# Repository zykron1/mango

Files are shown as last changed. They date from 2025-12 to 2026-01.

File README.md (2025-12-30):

# MANGO
An ESP32-S3 based flight computer with an external flash, imu, barometer, magnetometer, 4 servo ports, and 4 pyrotechnic channels with MOSFETs. Designed for Aerospace applications.
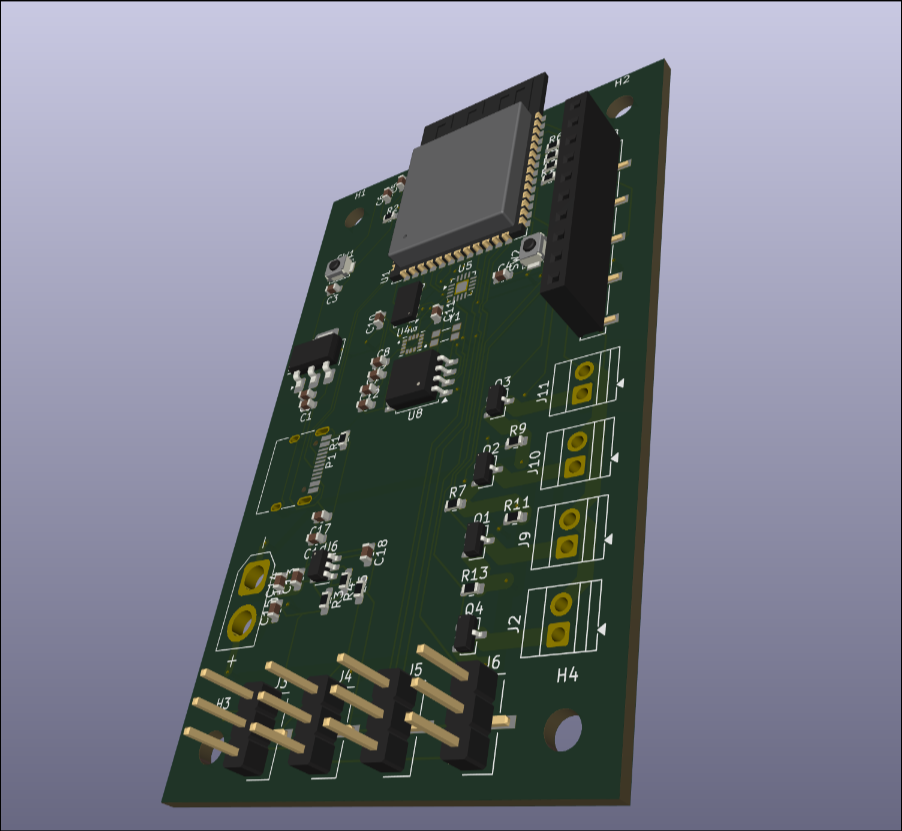
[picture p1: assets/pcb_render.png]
render


## Key Features
 - Dual core Xtensa microcontroller
 - 4 Servo Outputs
 - 4 High current mosfet switches for pyrotechnic channels
 - External 16 MB flash for flight logging
 - IMU, Magnetometer, and Barometer for orientation and state estimation
 - External expansion header with space for an I2C bus, 4 extra GPIO pins, and 2 pairs of power

## Schematic
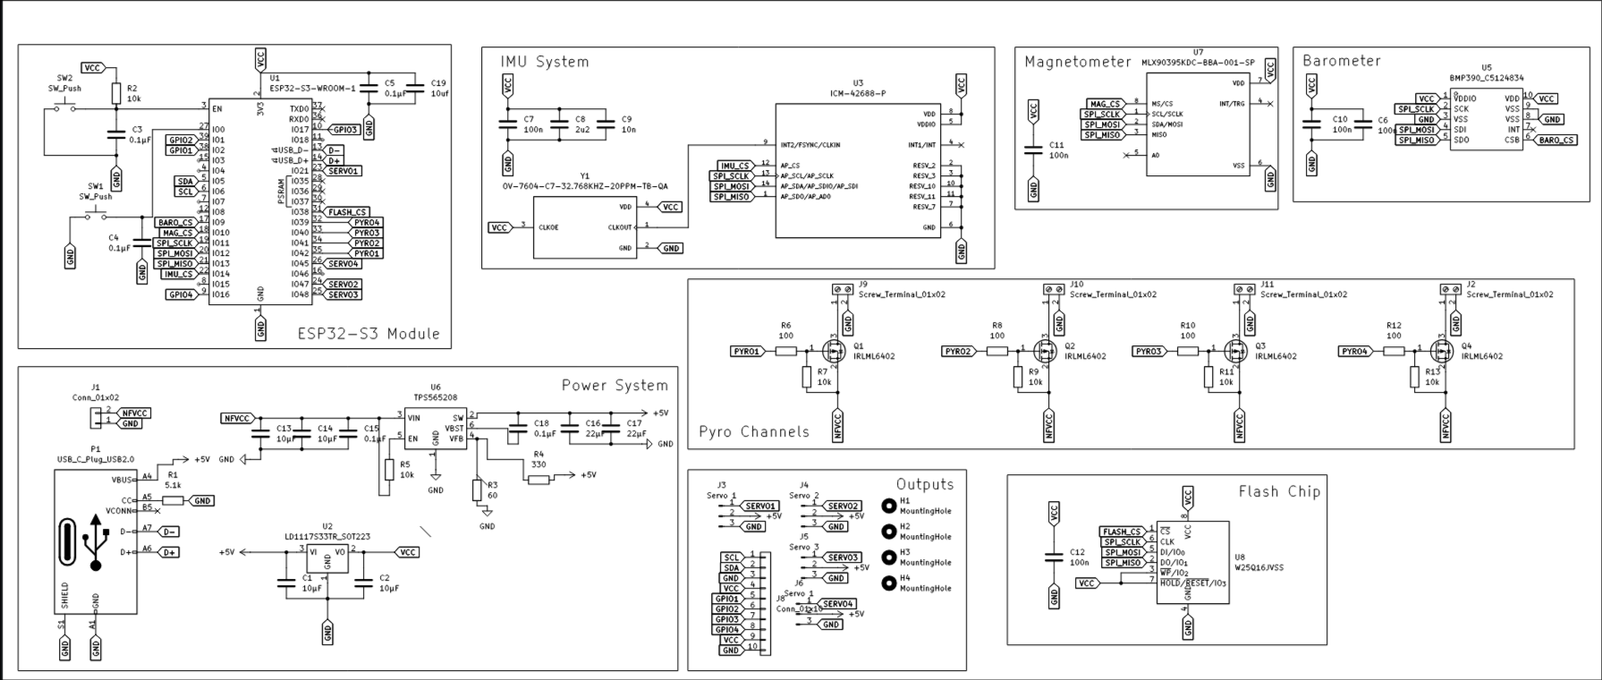
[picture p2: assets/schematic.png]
schematic


## PCB
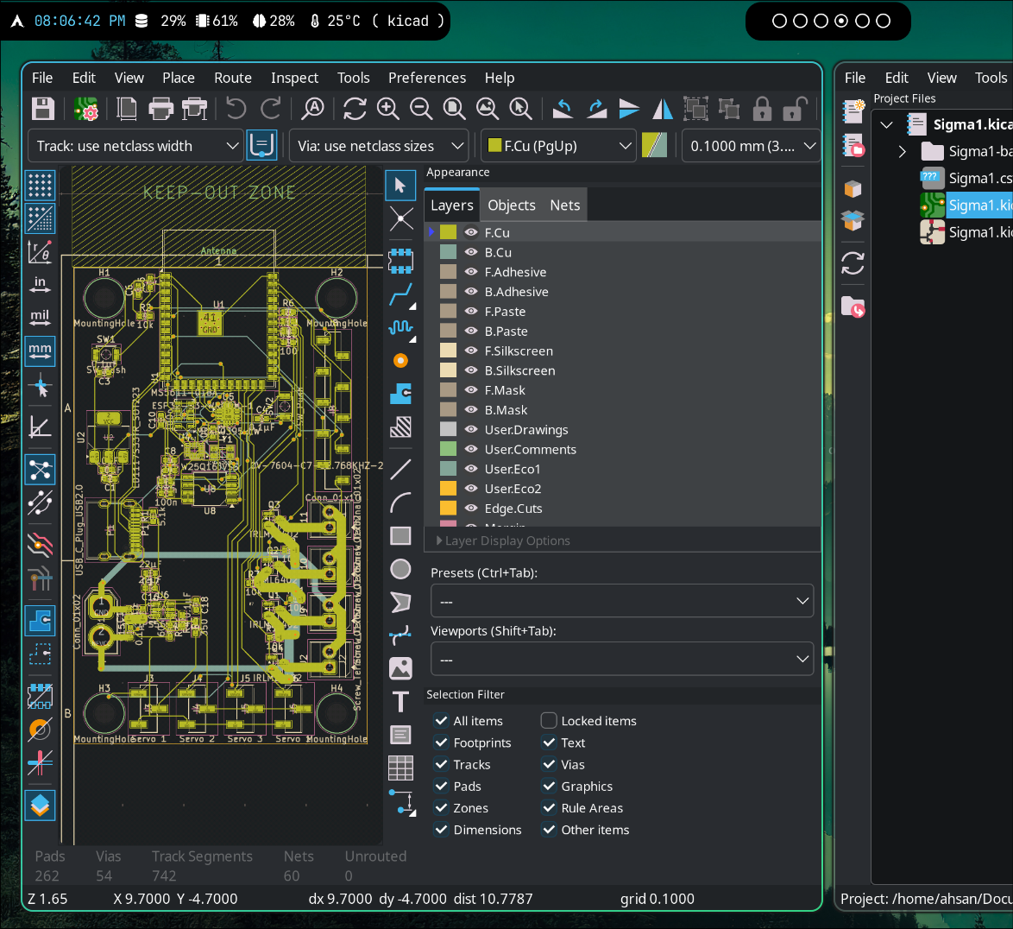
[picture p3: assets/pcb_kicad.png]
pcb


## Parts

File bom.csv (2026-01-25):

Product | Link | Cost Per Item | Quantity | Total | Note
(pcb AND STENCIL) | https://github.com/zykron1/mango/blob/main/pcb/production/MANGO_final.zip | $19.53 | 1 | $16.17
10µF | https://www.digikey.com/en/products/detail/murata-electronics/GRT188R61E106ME13D/5417024 | $0.25 | 4 | $1.00
100n | https://www.digikey.com/en/products/detail/murata-electronics/GCM188R71E104KA57D/3845251 | $0.25 | 5 | $1.25
0.1µF | https://www.digikey.com/en/products/detail/murata-electronics/GCM188R71E104KA57D/3845251 | $0.25 | 5 | $1.25
22µF | https://www.digikey.com/en/products/detail/yageo/CC0603MRX5R6BB226/5195721 | $0.65 | 2 | $1.30
10uf | https://www.digikey.com/en/products/detail/murata-electronics/GRT188R61E106ME13D/5417024 | $0.25 | 1 | $0.25
2u2 | https://www.digikey.com/en/products/detail/samsung-electro-mechanics/CL10B225KP8NNNC/3886792 | $0.08 | 1 | $0.08
10n | https://www.digikey.com/en/products/detail/murata-electronics/GRM1555C1E103JE01D/16707175 | $0.14 | 1 | $0.14
Conn_01x02 | https://www.digikey.com/en/products/detail/amphenol-icc-fci-/10129378-916001BLF/7915965 | $0.30 | 1 | $0.30
Screw_Terminal_01x02 | https://tinkersphere.com/breadboard-perfboard-prototyping/476-2-pole-screw-terminal-breadboard-compatible.html | $0.75 | 4 | $3.00 | Not requesting Funding for this
Servo 1 | sharing from 10 |  | 2 | 0
Servo 2 | sharing from 10 |  | 1 | 0
Servo 3 | sharing from 10 |  | 1 | 0
Conn_01x10 | sharing from 10 |  | 1 | 0
USB_C_Plug_USB2.0 | https://www.digikey.com/en/products/detail/amphenol-cs-commercial-products/124019772112A/13683231 | $1.96 | 1 | $1.96
IRLML6402 | https://www.digikey.com/en/products/detail/infineon-technologies/IRLML6402TRPBF/811437 | $0.42 | 4 | $1.68
5.1k | https://www.digikey.com/en/products/detail/yageo/RC0603FR-105K1L/14287630 | $0.10 | 1 | $0.10
100 | https://www.digikey.com/en/products/detail/yageo/RC0603FR-10100RL/12756410 | $0.10 | 4 | $0.40
<<<<<<< HEAD
10k | https://www.digikey.com/en/products/detail/yageo/RC0603FR-1010KL/12756418 | $0.10 | 6 | $0.60
60 | https://www.digikey.com/en/products/detail/bourns-inc/CR0603-FX-60R4ELF/CR0603-FX-60R4ELFCT-ND/4247821 | $0.10 | 1 | $0.10
330 | https://www.digikey.com/en/products/detail/vishay-dale/CRCW0603330RJNEAC/7928482 | $0.10 | 1 | $0.10
=======
10k | https://www.digikey.com/en/products/detail/yageo/RC0603FR-1010KL/12756418 | $0.10 | 7 | $0.70
3.3uh | https://www.digikey.com/en/products/detail/murata-electronics/LQM21PN3R3MG0D/19560375 | $0.17 | 1 | $0.17
54.9k | https://www.digikey.com/en/products/detail/yageo/RC0603FR-0754K9L/727298 | $0.10 | 1 | $0.10
>>>>>>> d75fabc (added inductor and used recomended texas instruments resistors)
TS-1088R-02026 | https://www.digikey.com/en/products/detail/e-switch/TL3365AF180QG/5964420 | $0.21 | 2 | $0.42
ESP32-S3-WROOM-1 | https://www.digikey.com/en/products/detail/espressif-systems/ESP32-S3-WROOM-1-N8/15200089 | $5.49 | 1 | $5.49
LD1117S33TR_SOT223 | https://www.digikey.com/en/products/detail/stmicroelectronics/LD1117S33TR/585766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 | $0.34 | 1 | $0.34
ICM-42688-P | https://www.digikey.com/en/products/detail/tdk-invensense/ICM-42688-P/10824934 | $4.67 | 1 | $4.67
BMP390_C5124834 | https://www.digikey.com/en/products/detail/bosch-sensortec/BMP390/16164575 | $3.15 | 1 | $3.15
TPS565208 | https://www.digikey.com/en/products/detail/texas-instruments/TPS565208DDCR/7776393 | $1.38 | 1 | $1.38
MLX90395KDC-BBA-001-SP | https://www.digikey.com/en/products/detail/melexis-technologies-nv/MLX90395KDC-BBA-101-RE/12330246 | $2.85 | 1 | $2.85
W25Q16JVSS | https://www.digikey.com/en/products/detail/winbond-electronics/W25Q16JVSSIQ/6193769 | $0.60 | 1 | $0.60
OV-7604-C7-32.768KHZ-20PPM-TB-QA | https://www.digikey.com/en/products/detail/micro-crystal-ag/OV-7604-C7-32-768KHZ-20PPM-TB-QA/10499163 | $2.07 | 1 | $2.07
Subtotal | $50.65
DigiKey Shipping Cost | $6.99
Digikey Tarrif Cost | $0.80
Total Parts Cost | $42.41 | (TAXES)
Total Board Cost | $58.58
Asking For: 62 dollars(JLC prices are variable)

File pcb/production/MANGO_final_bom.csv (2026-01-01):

Designator | Footprint | Quantity | Value | LCSC Part #
C1, C13, C14, C2 | 0603 | 4 | 10µF
C10, C11, C12, C6, C7 | 0603 | 5 | 100n
C15, C18, C3, C4, C5 | 0603 | 5 | 0.1µF
C16, C17 | 0603 | 2 | 22µF
C19 | 0603 | 1 | 10uf
C8 | 0603 | 1 | 2u2
C9 | 0603 | 1 | 10n
J1 | AMASS_XT30U-F_1x02_P5.0mm_Vertical | 1 | Conn_01x02
J10, J11, J2, J9 | TerminalBlock_Xinya_XY308-2.54-2P_1x02_P2.54mm_Horizontal | 4 | Screw_Terminal_01x02
J3, J6 | PinHeader_1x03_P2.54mm_Vertical | 2 | Servo 1
J4 | PinHeader_1x03_P2.54mm_Vertical | 1 | Servo 2
J5 | PinHeader_1x03_P2.54mm_Vertical | 1 | Servo 3
J8 | PinHeader_1x10_P2.54mm_Vertical | 1 | Conn_01x10
P1 | USB_C_Receptacle_Amphenol_124019772112A | 1 | USB_C_Plug_USB2.0
Q1, Q2, Q3, Q4 | SOT-23 | 4 | IRLML6402
R1 | 0603 | 1 | 5.1k
R10, R12, R6, R8 | 0603 | 4 | 100
R11, R13, R2, R5, R7, R9 | 0603 | 6 | 10k
R3 | 0603 | 1 | 60
R4 | 0603 | 1 | 330
SW1, SW2 | SW_TL3365AF180QG | 2 | SW_Push
U1 | ESP32-S3-WROOM-1 | 1 | ESP32-S3-WROOM-1
U2 | SOT-223-3_TabPin2 | 1 | LD1117S33TR_SOT223
U3 | PQFN50P300X250X97-14N | 1 | ICM-42688-P
U5 | LGA-10_L2.0-W2.0-P0.50-BL | 1 | BMP390_C5124834 | C5124834
U6 | SOT-23-6 | 1 | TPS565208
U7 | SOIC127P600X172-8N | 1 | MLX90395KDC-BBA-001-SP
U8 | SOIC-8_5.3x5.3mm_P1.27mm | 1 | W25Q16JVSS
Y1 | OSC_OV-7604-C7-32.768KHZ-20PPM-TB-QA | 1 | OV-7604-C7-32.768KHZ-20PPM-TB-QA

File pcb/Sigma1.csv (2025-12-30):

Reference | Qty | Value | DNP | Exclude from BOM | Exclude from Board | Footprint | Datasheet
C1,C2,C13,C14 | 4 | 10µF |  |  |  | Capacitor_SMD:C_0603_1608Metric | ~
C3,C4,C15,C18 | 4 | 0.1µF |  |  |  | Capacitor_SMD:C_0603_1608Metric | ~
C5,C6 | 2 | C |  |  |  | Capacitor_SMD:C_0603_1608Metric | ~
C7,C10,C11,C12 | 4 | 100n |  |  |  | Capacitor_SMD:C_0603_1608Metric | ~
C8 | 1 | 2u2 |  |  |  | Capacitor_SMD:C_0603_1608Metric | ~
C9 | 1 | 10n |  |  |  | Capacitor_SMD:C_0603_1608Metric | ~
C16,C17 | 2 | 22µF |  |  |  | Capacitor_SMD:C_0603_1608Metric | ~
H1,H2,H3,H4 | 4 | MountingHole |  | Excluded from BOM |  | MountingHole:MountingHole_3.2mm_M3 | ~
J1 | 1 | Conn_01x02 |  |  |  | Connector_AMASS:AMASS_XT30U-F_1x02_P5.0mm_Vertical | ~
J2,J9,J10,J11 | 4 | Screw_Terminal_01x02 |  |  |  | TerminalBlock:TerminalBlock_Xinya_XY308-2.54-2P_1x02_P2.54mm_Horizontal | ~
J3,J6 | 2 | Servo 1 |  |  |  | Connector_PinHeader_2.54mm:PinHeader_1x03_P2.54mm_Vertical_SMD_Pin1Left | ~
J4 | 1 | Servo 2 |  |  |  | Connector_PinHeader_2.54mm:PinHeader_1x03_P2.54mm_Vertical_SMD_Pin1Left | ~
J5 | 1 | Servo 3 |  |  |  | Connector_PinHeader_2.54mm:PinHeader_1x03_P2.54mm_Vertical_SMD_Pin1Left | ~
J8 | 1 | Conn_01x10 |  |  |  | Connector_PinSocket_2.54mm:PinSocket_1x10_P2.54mm_Vertical_SMD_Pin1Left | ~
P1 | 1 | USB_C_Plug_USB2.0 |  |  |  | Connector_USB:USB_C_Receptacle_HRO_TYPE-C-31-M-12 | https://www.usb.org/sites/default/files/documents/usb_type-c.zip
Q1,Q2,Q3,Q4 | 4 | IRLML6402 |  |  |  | Package_TO_SOT_SMD:SOT-23 | https://www.infineon.com/dgdl/irlml6402pbf.pdf?fileId=5546d462533600a401535668d5c2263c
R1 | 1 | 5.1k |  |  |  | Resistor_SMD:R_0603_1608Metric | ~
R2,R7,R9,R11,R13 | 5 | 10k |  |  |  | Resistor_SMD:R_0603_1608Metric | ~
R3 | 1 | 60 |  |  |  | Resistor_SMD:R_0603_1608Metric_Pad0.98x0.95mm_HandSolder | ~
R4 | 1 | 350 |  |  |  | Resistor_SMD:R_0603_1608Metric_Pad0.98x0.95mm_HandSolder | ~
R5 | 1 | 10k |  |  |  | Resistor_SMD:R_0603_1608Metric_Pad0.98x0.95mm_HandSolder | ~
R6,R8,R10,R12 | 4 | 100 |  |  |  | Resistor_SMD:R_0603_1608Metric | ~
SW1,SW2 | 2 | SW_Push |  |  |  | Button_Switch_SMD:SW_SPST_B3U-1000P-B | ~
U1 | 1 | ESP32-S3-WROOM-1 |  |  |  | RF_Module:ESP32-S3-WROOM-1 | https://www.espressif.com/sites/default/files/documentation/esp32-s3-wroom-1_wroom-1u_datasheet_en.pdf
U2 | 1 | LD1117S33TR_SOT223 |  |  |  | Package_TO_SOT_SMD:SOT-223-3_TabPin2 | http://www.st.com/st-web-ui/static/active/en/resource/technical/document/datasheet/CD00000544.pdf
U3 | 1 | ICM-42688-P |  |  |  | ICM:PQFN50P300X250X97-14N
U4 | 1 | MS5611-01BA |  |  |  | Package_LGA:LGA-8_3x5mm_P1.25mm | https://www.te.com/commerce/DocumentDelivery/DDEController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
U5 | 1 | MLX90395xLW |  |  |  | Package_DFN_QFN:QFN-16-1EP_3x3mm_P0.5mm_EP1.675x1.675mm | https://www.melexis.com/en/documents/documentation/datasheets/datasheet-mlx90395
U6 | 1 | TPS565208 |  |  |  | Package_TO_SOT_SMD:SOT-23-6 | http://www.ti.com/lit/ds/symlink/tps565208.pdf
U8 | 1 | W25Q16JVSS |  |  |  | Package_SO:SOIC-8_5.3x5.3mm_P1.27mm | https://www.winbond.com/hq/support/documentation/levelOne.jsp?__locale=en&DocNo=DA00-W25Q16JV.1
Y1 | 1 | OV-7604-C7-32.768KHZ-20PPM-TB-QA |  |  |  | OV7604C7:OSC_OV-7604-C7-32.768KHZ-20PPM-TB-QA

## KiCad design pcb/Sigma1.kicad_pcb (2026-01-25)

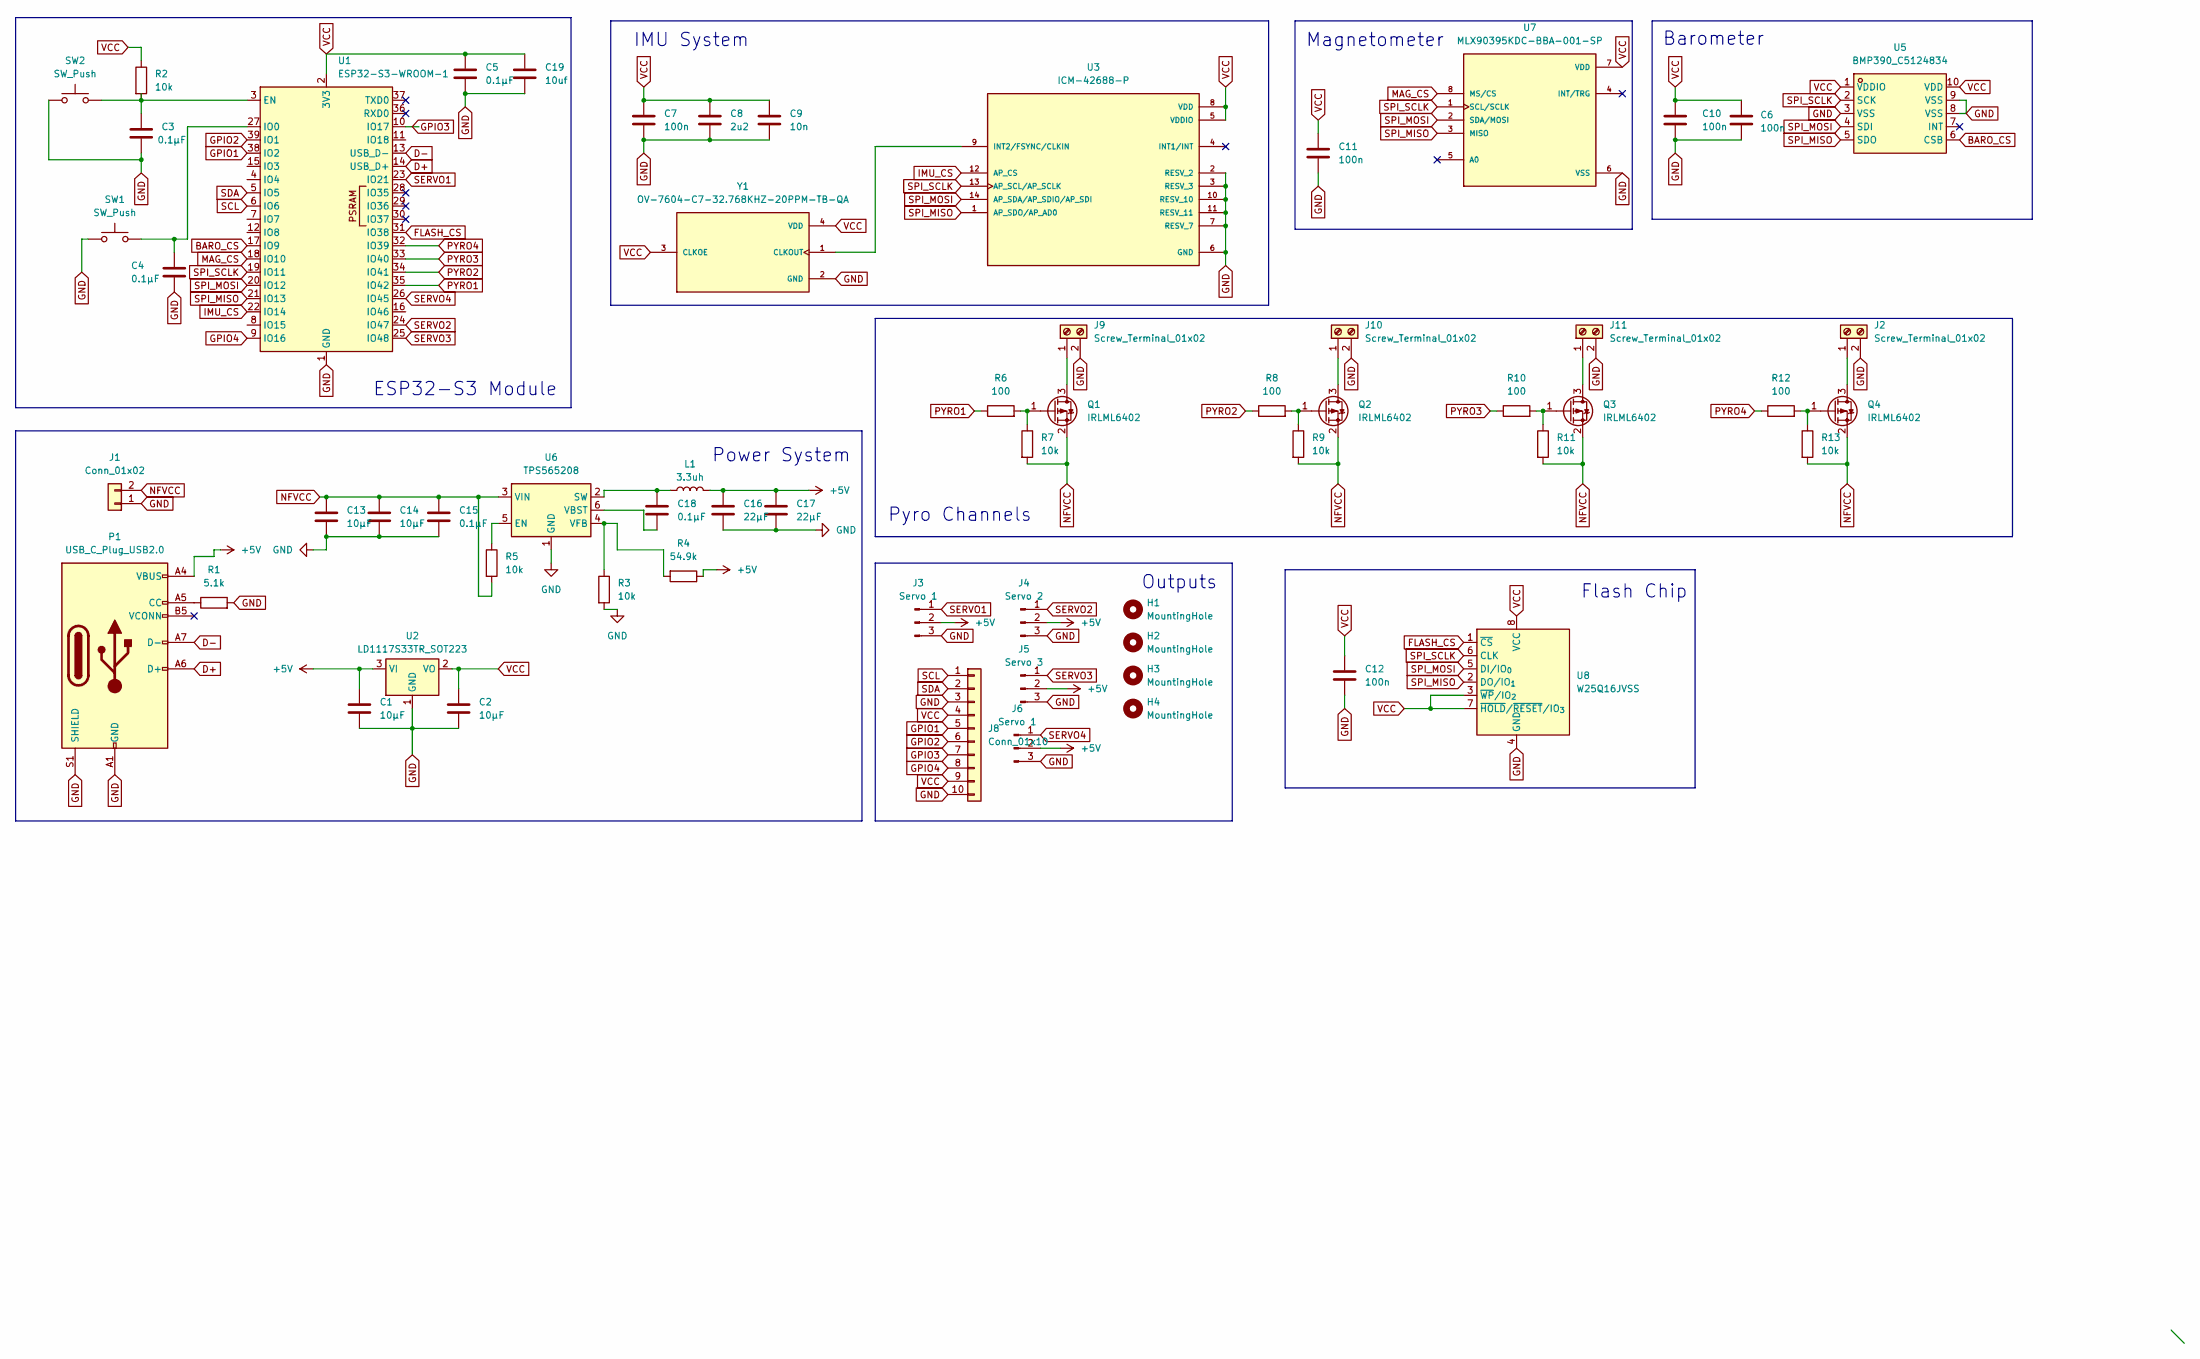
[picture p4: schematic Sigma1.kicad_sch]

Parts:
C1, C2, C13, C14: 10µF; C_0603_1608Metric
C3, C4, C15, C18: 0.1µF; C_0603_1608Metric
C5: 0.1μF; C_0603_1608Metric
C6, C7, C10, C11, C12: 100n; C_0603_1608Metric
C8: 2u2; C_0603_1608Metric
C9: 10n; C_0603_1608Metric
C16, C17: 22µF; C_0603_1608Metric
C19: 10uf; C_0603_1608Metric
H1, H2, H3, H4: MountingHole; MountingHole_3.2mm_M3
J1: Conn_01x02; AMASS_XT30U-F_1x02_P5.0mm_Vertical
J2, J9, J10, J11: Screw_Terminal_01x02; TerminalBlock_Xinya_XY308-2.54-2P_1x02_P2.54mm_Horizontal
J3, J6: Servo 1; PinHeader_1x03_P2.54mm_Vertical
J4: Servo 2; PinHeader_1x03_P2.54mm_Vertical
J5: Servo 3; PinHeader_1x03_P2.54mm_Vertical
J8: Conn_01x10; PinHeader_1x10_P2.54mm_Vertical
L1: 3.3uh; L_0805_2012Metric
P1: USB_C_Plug_USB2.0; USB_C_Receptacle_Amphenol_124019772112A
Q1, Q2, Q3, Q4: IRLML6402; SOT-23
R1: 5.1k; R_0603_1608Metric
R2, R7, R9, R11, R13: 10k; R_0603_1608Metric
R3, R5: 10k; R_0603_1608Metric_Pad0.98x0.95mm_HandSolder
R4: 54.9k; R_0603_1608Metric_Pad0.98x0.95mm_HandSolder
R6, R8, R10, R12: 100; R_0603_1608Metric
SW1, SW2: SW_Push; SW_TL3365AF180QG
U1: ESP32-S3-WROOM-1
U2: LD1117S33TR_SOT223; SOT-223-3_TabPin2
U3: ICM-42688-P; PQFN50P300X250X97-14N; PARTREV 1.2
U5: BMP390_C5124834; LGA-10_L2.0-W2.0-P0.50-BL; LCSC Part C5124834
U6: TPS565208; SOT-23-6
U7: MLX90395KDC-BBA-001-SP; SOIC127P600X172-8N; PARTREV 6.0
U8: W25Q16JVSS; SOIC-8_5.3x5.3mm_P1.27mm
Y1: OV-7604-C7-32.768KHZ-20PPM-TB-QA; OSC_OV-7604-C7-32.768KHZ-20PPM-TB-QA; PARTREV 4.4

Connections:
+5V: C1.1, C16.1, C17.1, J3.2, J4.2, J5.2, J6.2, L1.1, P1.A4 (VBUS), P1.A9 (VBUS), P1.B4 (VBUS), P1.B9 (VBUS), R4.1, U2.3 (VI)
BARO_CS: U1.17 (IO9), U5.6 (CSB)
D+: P1.A6 (D+), U1.14 (USB_D+)
D-: P1.A7 (D-), U1.13 (USB_D-)
FLASH_CS: U1.31 (IO38), U8.1 (~CS)
GND: C1.2, C2.2, C3.2, C4.2, C5.2, C6.2, C7.2, C8.2, C9.2, C10.2, C11.2, C12.2, C13.2, C14.2, C15.2, C16.2, C17.2, C19.2, J1.1, J2.2, J3.3, J4.3, J5.3, J6.3, J8.3, J8.10, J9.2, J10.2, J11.2, P1.A1 (GND), P1.A12 (GND), P1.B1 (GND), P1.B12 (GND), P1.S1 (SHIELD), R1.2, R3.2, SW1.1, SW2.1, U1.1 (GND), U1.40 (GND), U1.41 (GND), U2.1 (GND), U3.2 (RESV_2), U3.3 (RESV_3), U3.6 (GND), U3.7 (RESV_7), U3.10 (RESV_10), U3.11 (RESV_11), U5.3 (VSS), U5.8 (VSS), U5.9 (VSS), U6.1 (GND), U7.6 (VSS), U8.4 (GND), Y1.2 (GND)
GPIO1: J8.5, U1.38 (IO2)
GPIO2: J8.6, U1.39 (IO1)
GPIO3: J8.7, U1.10 (IO17)
GPIO4: J8.8, U1.9 (IO16)
IMU_CS: U1.22 (IO14), U3.12 (AP_CS)
MAG_CS: U1.18 (IO10), U7.8 (MS/CS)
NFVCC: C13.1, C14.1, C15.1, J1.2, Q1.2 (S), Q2.2 (S), Q3.2 (S), Q4.2 (S), R5.2, R7.2, R9.2, R11.2, R13.2, U6.3 (VIN)
unnamed: J2.1, Q4.3 (D)
unnamed: J9.1, Q1.3 (D)
unnamed: J10.1, Q2.3 (D)
unnamed: J11.1, Q3.3 (D)
unnamed: P1.A5 (CC), R1.1
unnamed: Q1.1 (G), R6.2, R7.1
unnamed: Q2.1 (G), R8.2, R9.1
unnamed: Q3.1 (G), R10.2, R11.1
unnamed: Q4.1 (G), R12.2, R13.1
unnamed: C3.1, R2.2, SW2.2, U1.3 (EN)
unnamed: C4.1, SW1.2, U1.27 (IO0)
unnamed: U3.9 (INT2/FSYNC/CLKIN), Y1.1 (CLKOUT)
unnamed: R5.1, U6.5 (EN)
unnamed: C18.1, L1.2, U6.2 (SW)
unnamed: C18.2, U6.6 (VBST)
unnamed: R3.1, R4.2, U6.4 (VFB)
PYRO1: R6.1, U1.35 (IO42)
PYRO2: R8.1, U1.34 (IO41)
PYRO3: R10.1, U1.33 (IO40)
PYRO4: R12.1, U1.32 (IO39)
SCL: J8.1, U1.6 (IO6)
SDA: J8.2, U1.5 (IO5)
SERVO1: J3.1, U1.23 (IO21)
SERVO2: J4.1, U1.24 (IO47)
SERVO3: J5.1, U1.25 (IO48)
SERVO4: J6.1, U1.26 (IO45)
SPI_MISO: U1.21 (IO13), U3.1 (AP_SDO/AP_AD0), U5.5 (SDO), U7.3 (MISO), U8.2 (DO/IO_{1})
SPI_MOSI: U1.20 (IO12), U3.14 (AP_SDA/AP_SDIO/AP_SDI), U5.4 (SDI), U7.2 (SDA/MOSI), U8.5 (DI/IO_{0})
SPI_SCLK: U1.19 (IO11), U3.13 (AP_SCL/AP_SCLK), U5.2 (SCK), U7.1 (SCL/SCLK), U8.6 (CLK)
VCC: C2.1, C5.1, C6.1, C7.1, C8.1, C9.1, C10.1, C11.1, C12.1, C19.1, J8.4, J8.9, R2.1, U1.2 (3V3), U2.2 (VO), U3.5 (VDDIO), U3.8 (VDD), U5.1 (VDDIO), U5.10 (VDD), U7.7 (VDD), U8.3 (~WP/IO_{2}), U8.7 (~HOLD/~RESET/IO_{3}), U8.8 (VCC), Y1.3 (CLKOE), Y1.4 (VDD)

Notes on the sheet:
ESP32-S3 Module
Flash Chip
Magnetometer
Outputs
Pyro Channels
Power System
Barometer
IMU System

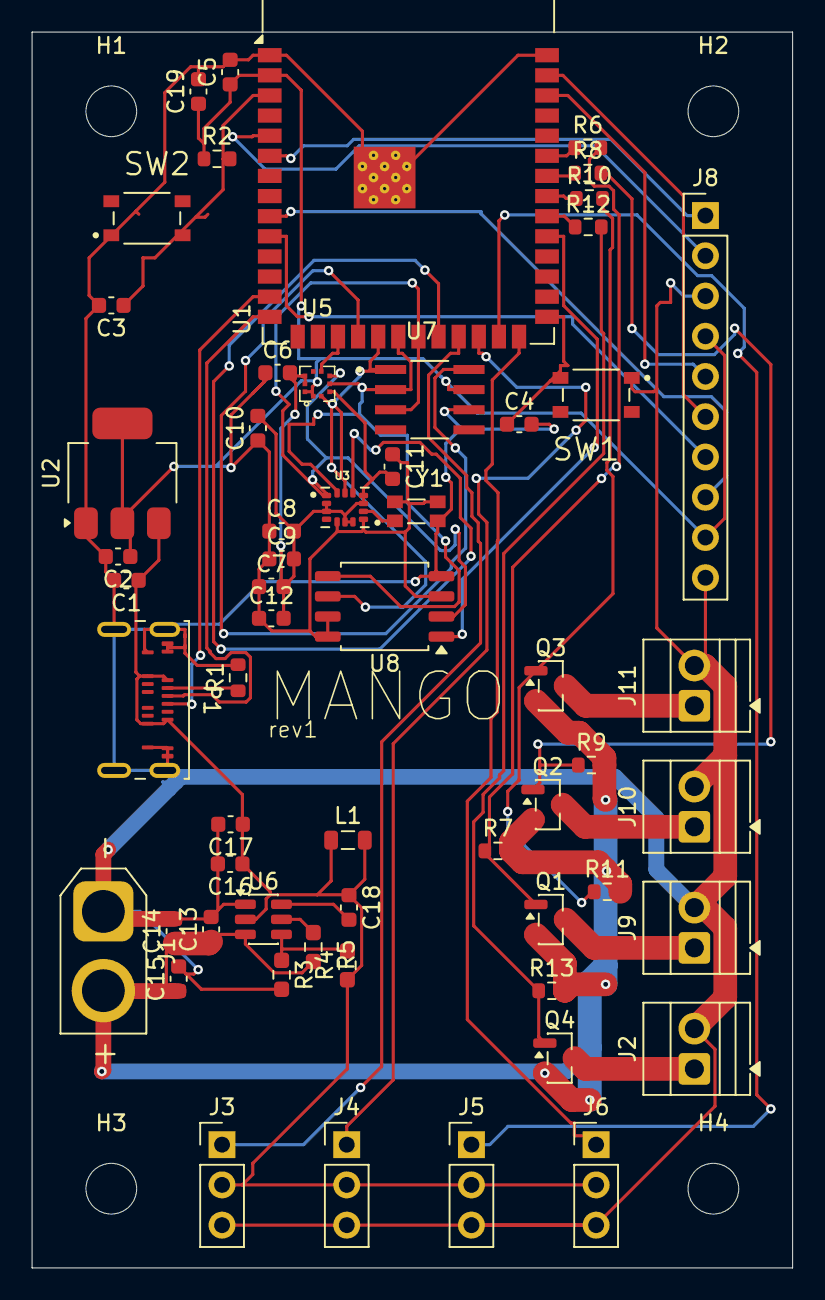
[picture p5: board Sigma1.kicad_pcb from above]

Board: 2 copper layers, 48.0 x 78.0 mm, 62 parts (0 on the bottom side), 43 nets.

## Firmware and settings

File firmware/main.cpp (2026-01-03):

#include <Arduino.h>
#include "drivers/icm42688p.h"
#include "drivers/SG90Servo.h"
#include "pid.h"

#define MOTOR_FL 3
#define MOTOR_FR 5
#define MOTOR_BL 6
#define MOTOR_BR 9

ICM42688P imu;

SG90Servo mFL(MOTOR_FL);
SG90Servo mFR(MOTOR_FR);
SG90Servo mBL(MOTOR_BL);
SG90Servo mBR(MOTOR_BR);

PID pidRoll(1.2f, 0.0f, 0.04f);
PID pidPitch(1.2f, 0.0f, 0.04f);
PID pidYaw(1.0f, 0.0f, 0.02f);

float roll = 0.0f;
float pitch = 0.0f;
float yaw = 0.0f;

unsigned long lastMicros = 0;

void setup() {
	imu.begin();

	mFL.begin();
	mFR.begin();
	mBL.begin();
	mBR.begin();

	pidRoll.setSetpoint(0.0f);
	pidPitch.setSetpoint(0.0f);
	pidYaw.setSetpoint(0.0f);

	pidRoll.setOutputLimits(-30, 30);
	pidPitch.setOutputLimits(-30, 30);
	pidYaw.setOutputLimits(-20, 20);

	lastMicros = micros();
}

void loop() {
	mFL.update();
	mFR.update();
	mBL.update();
	mBR.update();

	unsigned long now = micros();
	float dt = (now - lastMicros) * 1e-6f;
	lastMicros = now;

	int16_t gx, gy, gz;
	if (!imu.readGyro(gx, gy, gz)) return;

	float gyroX = gx * 0.000266f;
	float gyroY = gy * 0.000266f;
	float gyroZ = gz * 0.000266f;

	roll  += gyroX * dt;
	pitch += gyroY * dt;
	yaw   += gyroZ * dt;

	float rollOut  = pidRoll.update(roll, dt);
	float pitchOut = pidPitch.update(pitch, dt);
	float yawOut   = pidYaw.update(yaw, dt);

	int base = 90;

	mFL.write(base + pitchOut + rollOut - yawOut);
	mFR.write(base + pitchOut - rollOut + yawOut);
	mBL.write(base - pitchOut + rollOut + yawOut);
	mBR.write(base - pitchOut - rollOut - yawOut);
}

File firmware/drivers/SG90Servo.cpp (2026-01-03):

#include "SG90Servo.h"

/* 
 Can be refactored to use for ESC's
 * */

SG90Servo::SG90Servo(uint8_t pin)
	: _pin(pin), _pulse(1500), _last(0) {}

void SG90Servo::begin() {
	pinMode(_pin, OUTPUT);
	digitalWrite(_pin, LOW);
}

void SG90Servo::write(uint8_t angle) {
	angle = constrain(angle, 0, 180);
	_pulse = map(angle, 0, 180, 500, 2400);
}

void SG90Servo::writeMicroseconds(uint16_t us) {
	_pulse = constrain(us, 500, 2400);
}

void SG90Servo::update() {
	unsigned long now = micros();
	if (now - _last >= 20000) {
		_last = now;
		digitalWrite(_pin, HIGH);
		delayMicroseconds(_pulse);
		digitalWrite(_pin, LOW);
	}
}

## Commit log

2025-12-31 supply chain changes
    [BOM.csv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]
2025-12-31 drc fixes
    [Sigma1.kicad_pcb]
2025-12-31 BOM + supply chain changes
    [Sigma1.kicad_pcb, Sigma1.kicad_sch, bom.csv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]
2026-01-01 final commit
    [MANGO_final_bom.csv, MANGO_final_designators.csv, MANGO_final_positions.csv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]
2026-01-03 extremely rought basic firmware for drone with MMU, pid, and sensor loop control. arduino cpp
2026-01-03 Revise bom.csv with updated product details
    Updated bill of materials with new links and costs.
    [bom.csv]
2026-01-03 fixed price
    [bom.csv]
2026-01-25 fix conflict?
    [Sigma1.kicad_pcb, Sigma1.kicad_sch, bom.csv]
